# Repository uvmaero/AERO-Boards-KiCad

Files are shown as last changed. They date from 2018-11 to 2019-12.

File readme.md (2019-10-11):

# Readme

This repo was originally @willemcvu 's personal AERO boards repo. From 2019-20 onward it will be used by all of AERO to store boards designed for the AERO cars.

Some are finished and have been produced, tested, etc. Others have not. Up to you to figure out if a particular board might be useful for your needs.

If you do produce a board, let me know! I'd love to know what you're using it for.

Everything here is licensed under CC-BY-SA and thus is OSHWA-compliant.

# The Boards

(Often out-of-date) descriptions of what these boards do.

## BattMon

Monitors the current/voltage to/from a battery and power consumer. Includes a relay on the battery, ATMega328p, and CANBUS interface. This board has been produced and partially tested.
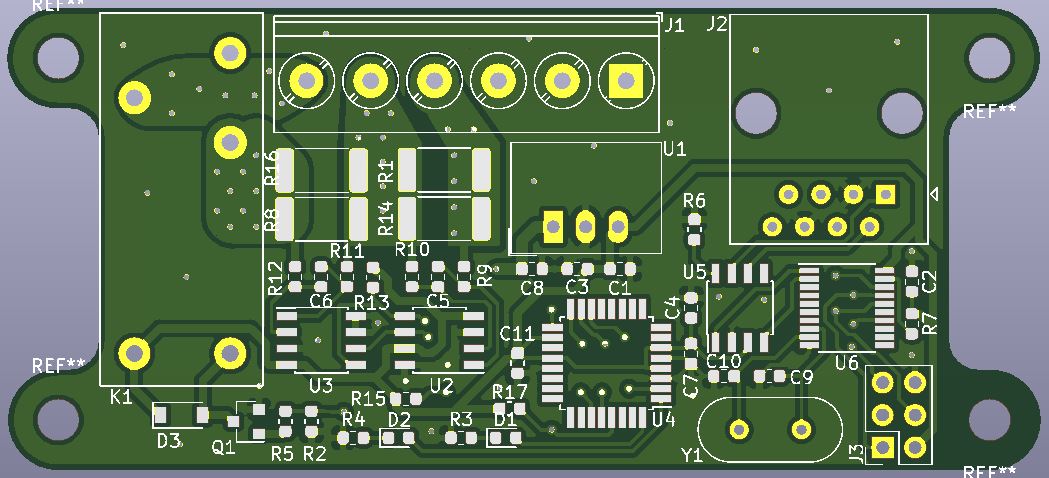
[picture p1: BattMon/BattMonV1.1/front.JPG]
Front BattMon

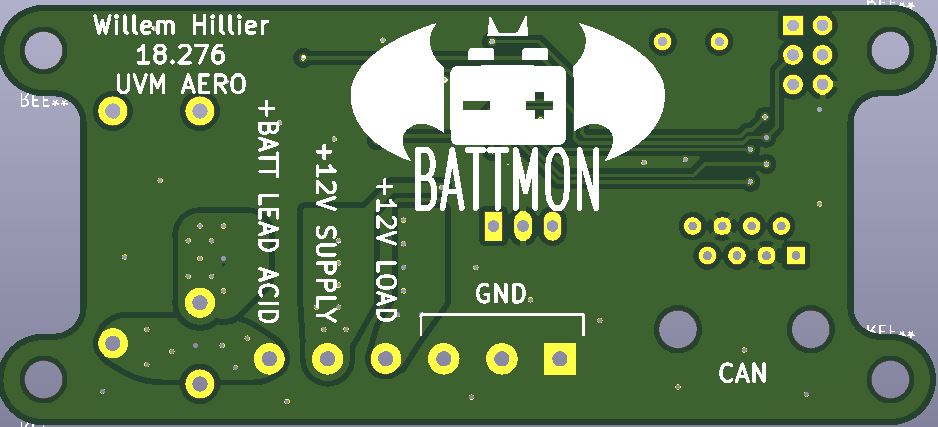
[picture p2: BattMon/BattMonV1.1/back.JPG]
Back BattMon


## CANShield
A generic Arduino Uno CANBUS shield. Once hooked up to an Uno, it is the same circuit used for all the boards with CANBUS+ATMega328p found here. Untested and unproduced.
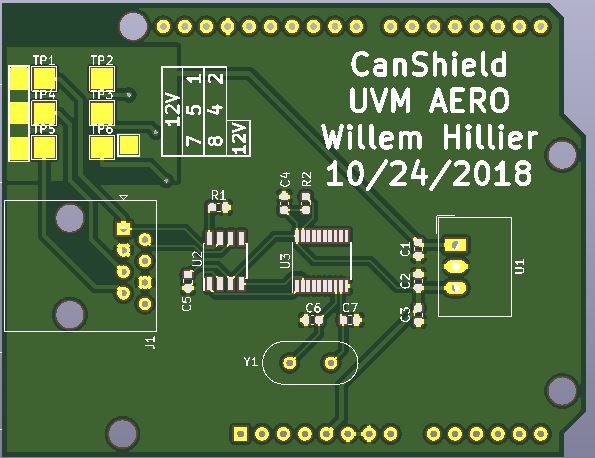
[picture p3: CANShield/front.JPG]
Front CanShield

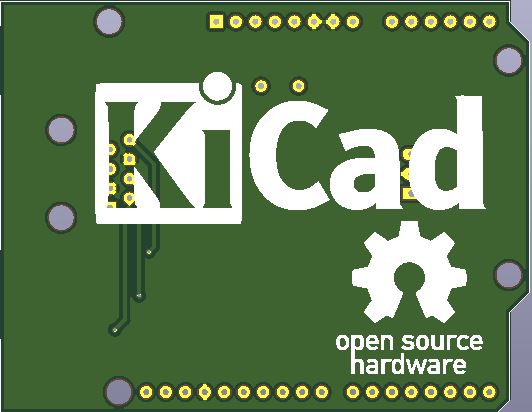
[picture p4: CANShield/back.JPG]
Back CanShield


## DC_DCBoard - Superseded by interface-board ("BigBoi")
Converts ~300VDC to ~12VDC using a DCM CHiP module from Vicor Power. Can do 400W peak, will dissapate almost 40W at that load, so it has a 19mm Vicor heatsink, model #(?can't remember).  Version 1 has clearance issues. Version 2 is an intermediate version with those issues mostly fixed. Version 3 is still be designed, and it will be the final version. None have been produced or tested, and all probably have issues (v1 and v2 have known issues, and v3 isn't finished).
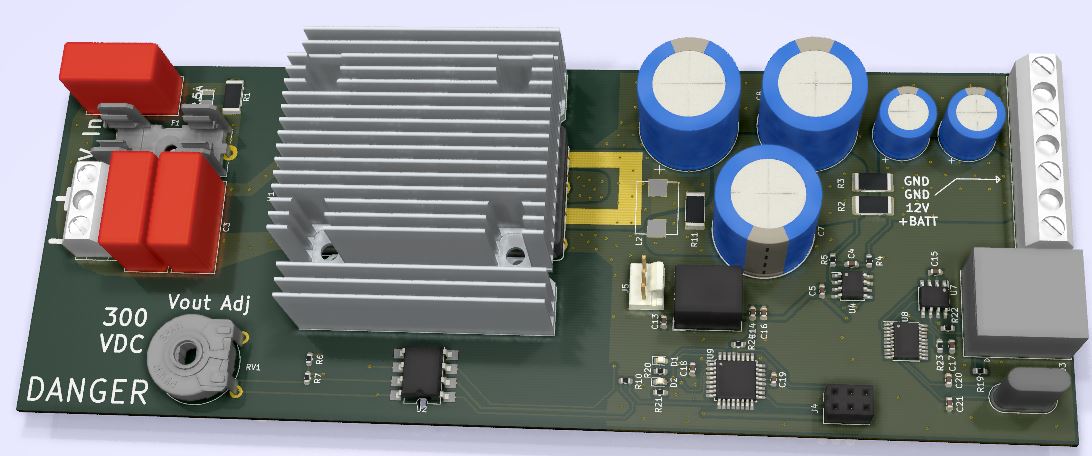
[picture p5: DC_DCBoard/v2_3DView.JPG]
DC_DCBoard


## FanBoy - Superseded by interface-board ("BigBoi")
Simple 4-channel PWM fan controller with ATMega328p and CANBUS interface. Tested, works great. Should be able to do ~15A a channel, although this hasn't been tested, and is probably not recommended.
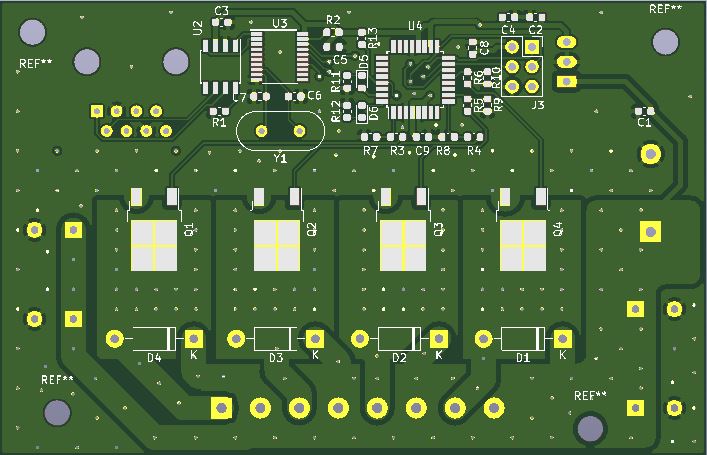
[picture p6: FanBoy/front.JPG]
Front FanBoy

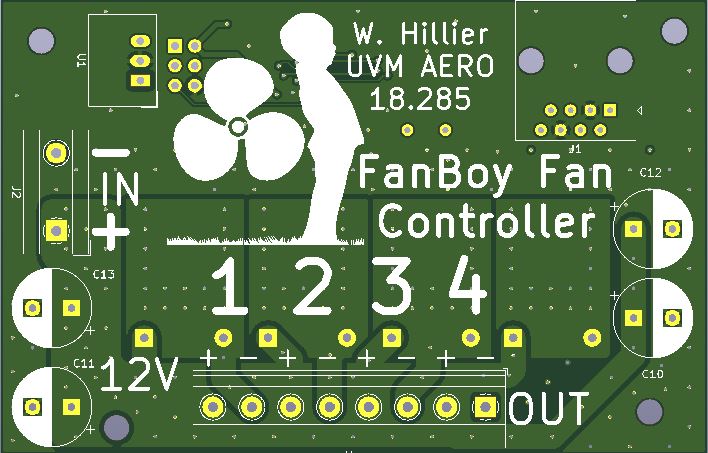
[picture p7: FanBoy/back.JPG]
Back FanBoy


## interface-board (aka "BigBoi")
Contains all the high-voltage interface circuitry. Hosts a Vicor DC/DC converter module that generates 12V for the entire car. Also controls fans, pump, and brakelight, and includes CANBUS interface, NTC inputs, and some assorted other functionality. "standoffs-biggerbox" is the current working version. Competition-tested, working 100%.
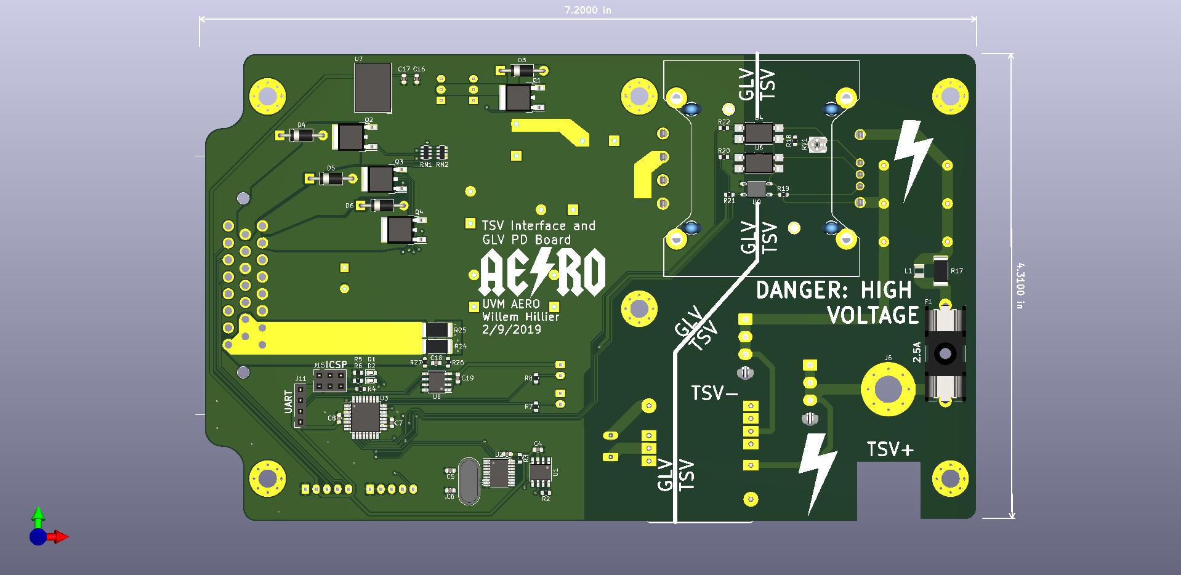
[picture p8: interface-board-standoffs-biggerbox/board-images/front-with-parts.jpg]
bigboi front


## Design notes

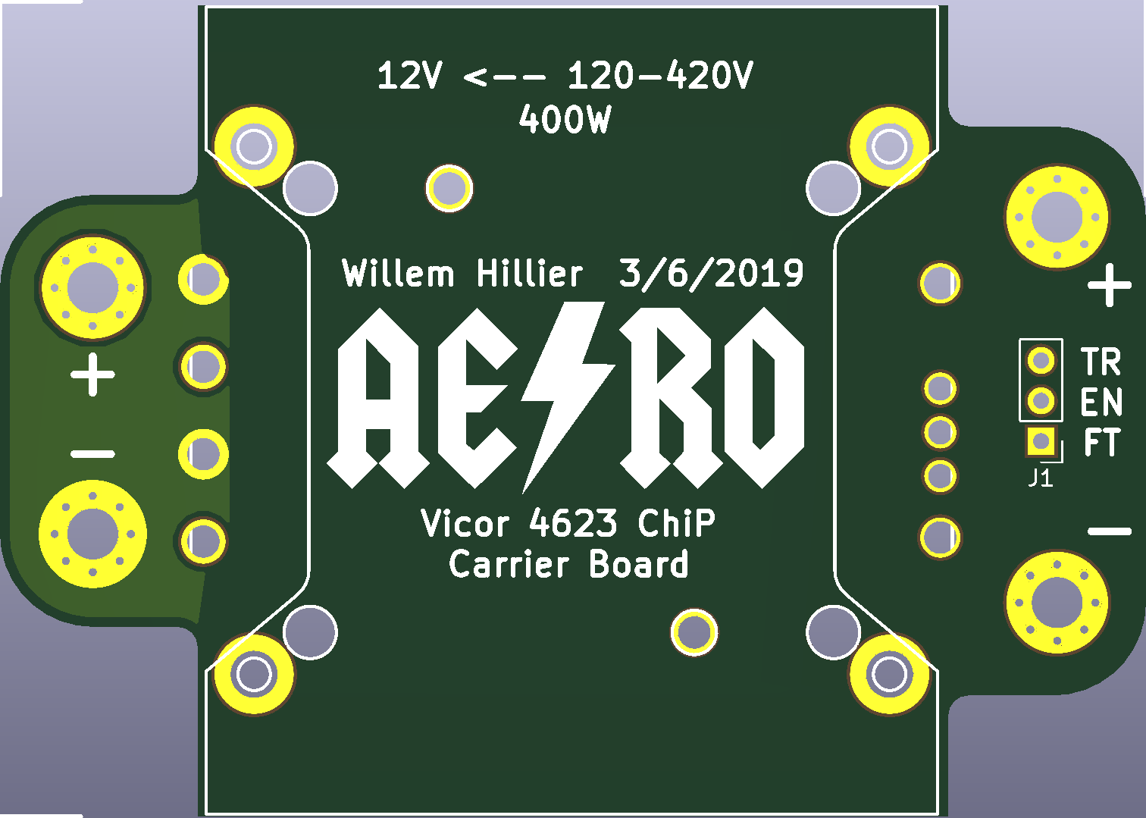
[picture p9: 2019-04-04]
vicor-socket/back.PNG

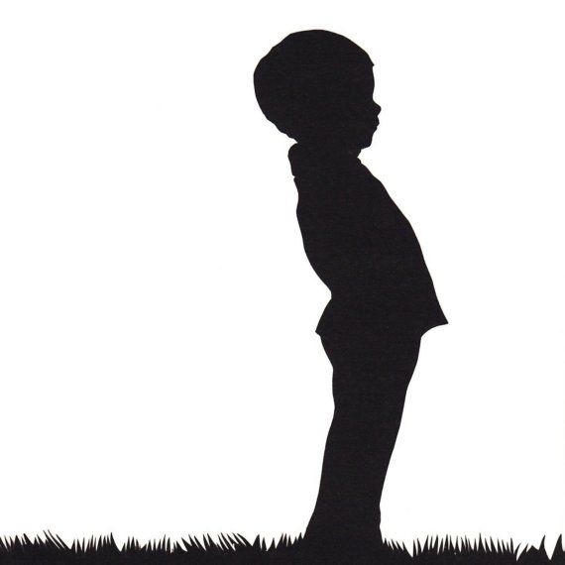
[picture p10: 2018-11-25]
FanBoy/boy.jpg

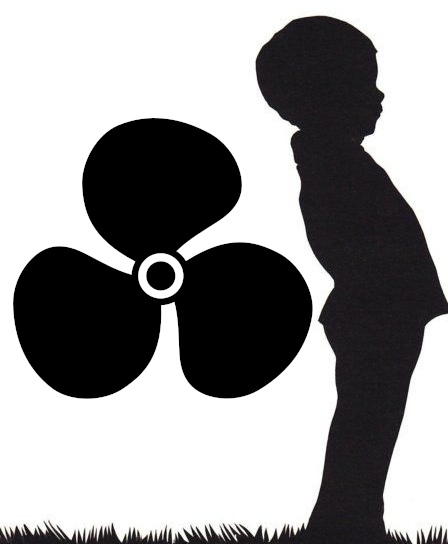
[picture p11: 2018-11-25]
FanBoy/fanboy.png

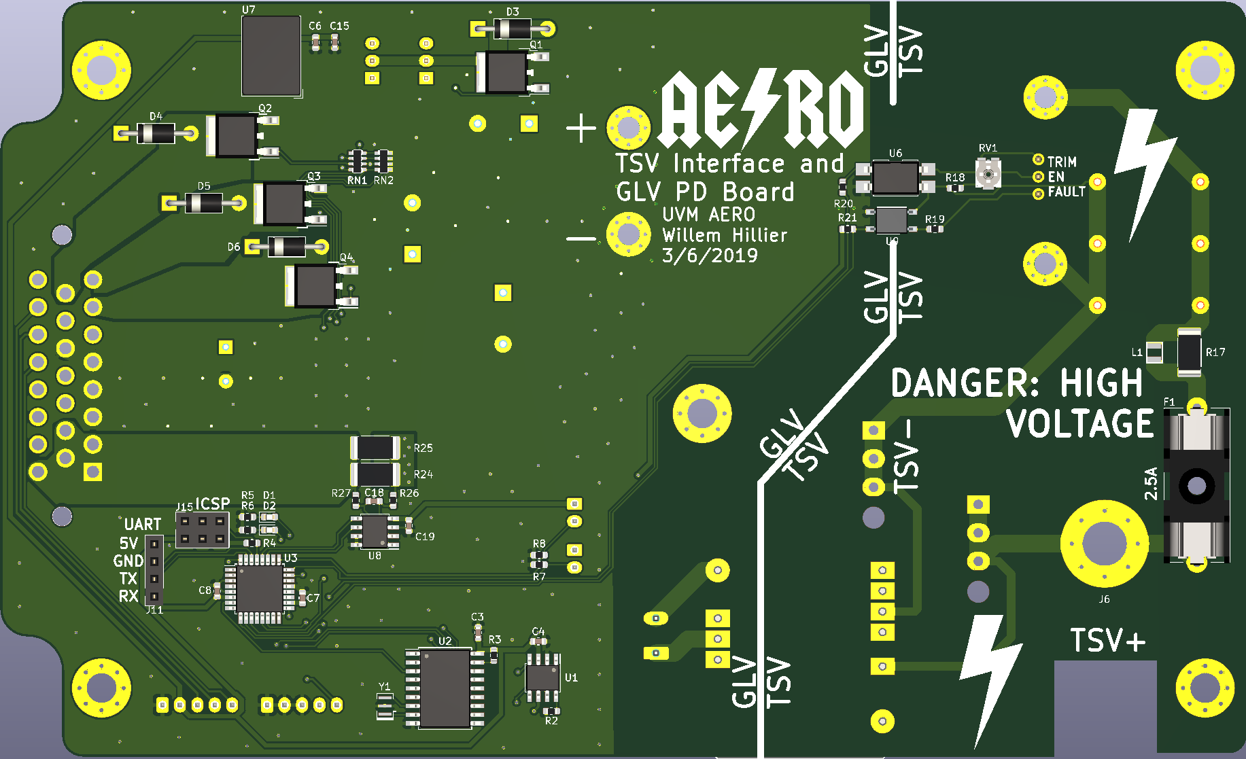
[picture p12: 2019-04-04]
interface-board-standoffs-biggerbox/front.PNG

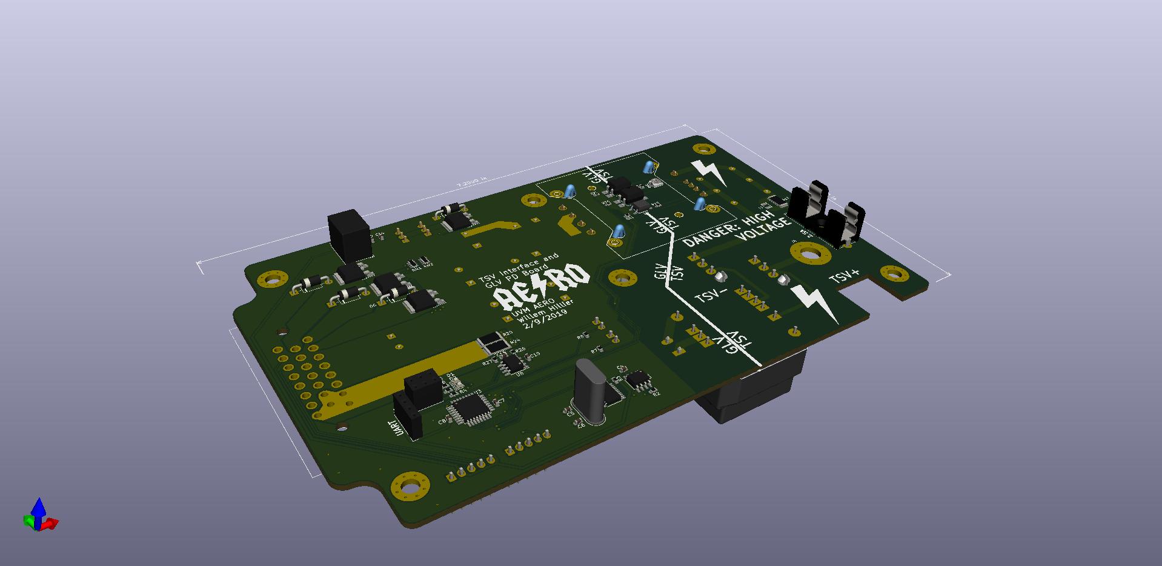
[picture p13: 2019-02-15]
interface-board-standoffs-biggerbox/board-images/front-3d.jpg

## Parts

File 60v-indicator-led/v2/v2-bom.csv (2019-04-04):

Id | Designator | Package | Quantity | Designation | Supplier and ref
1 | G***,G*** | AERO_Logo_15x6mm | 2 | LOGO
2 | D1 | LPA-C011301S-x LED 0805 LIGHT PIPE SINGLE VERT SMD | 1 | RED_LED
3 | R1,R2,R3,R4,R5,R6,R7,R8,R9,R10 | R_0805_2012Metric | 10 | 1k
4 | M3 | MountingHole_3.2mm_M3_DIN965 | 1 | MountingHole_3.2mm_M3_DIN965
5 | J1,J2 | TE_MATE-N-LOK_1-770866-x_1x02_P4.14mm_Vertical | 2 | Conn_01x02

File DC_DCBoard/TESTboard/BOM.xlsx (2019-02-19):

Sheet: Sheet1
Vendor | Found? | Digikey | Mouser | MPN | Quantity | ref | value5 | footprint | lib | part | description | names | tstamps6 | tstamp | datasheet | lib7 | part8 | description9 | docs | fp | field | name10 | num | name11 | type | alias | logical | uri | code | name12 | ref13 | pin
 | x |  |  |  | 1 | U1 | DCM4623TD2J13D0T70 | CustomFootprints:DCM4623TD2J13D0T70 w_landpattern | DC_DCBoard-rescue | DCM4623TD2J13D0T70-AEROParts |  | / | / | 5BDD1F41
 |  |  |  |  | 1 | R1 | 1Ω | Resistor_SMD:R_2512_6332Metric | Device | R_US | Resistor US symbol | / | / | 5BDD239A | ~
 | x |  |  | DFE252012P-1R0M=P2 | 1 | L1 | 1uH | CustomFootprints:Murata_DFE252012P_Inductor | Device | L_Small | Inductor, small symbol | / | / | 5BDD2418 | ~
 | x |  | https://www.mouser.com/ProductDetail/EPCOS-TDK/B32672P5684K000?qs=vvQZUlcHev%2F7kTLX0LjBgw%3D%3D | B32672P5684K000 | 3 | C1 | 0.68uF | Capacitor_THT:C_Rect_L18.0mm_W8.0mm_P15.00mm_FKS3_FKP3 | Device | C_Small | Unpolarized capacitor | / | / | 5BDD25B3 | ~
AERO | x |  |  |  | 3 | R6 | 1k | Resistor_SMD:R_0603_1608Metric | Device | R_US | Resistor US symbol | / | / | 5BDD58DC | ~
AERO | x |  |  |  | 1 | R9 | 10k | Resistor_SMD:R_0603_1608Metric | Device | R_US | Resistor US symbol | / | / | 5BDDACE2 | ~
AERO | x |  |  |  | 2 | C9 | 470uF | Capacitor_THT:CP_Radial_D10.0mm_P5.00mm | Device | C | Unpolarized capacitor | / | / | 5BDDF5C4 | ~
 | x |  |  | TC33X-2-503E | 1 | RV1 | 50k | CustomFootprints:TC33X-503ECT-ND | Device | R_POT_TRIM_US | Trim-Potentiometer US symbol | / | / | 5BF39F9A | ~
 |  |  |  | PA2607.151NLT | 1 | L2 | 0.15uH | CustomFootprints:PA2607 | Device | L_Small | Inductor, small symbol | / | / | 5BEEF7F2 | ~
 |  |  |  |  |  | R11 | 1Ω | Resistor_SMD:R_2512_6332Metric | Device | R_US | Resistor US symbol | / | / | 5BEF82F3 | ~
 |  |  |  |  | 3 | C6 | 4700uF | Capacitor_THT:CP_Radial_D18.0mm_P7.50mm | Device | C_Small | Unpolarized capacitor | / | / | 5BF35C23 | ~
 |  |  |  |  |  | J1 | TSV | TerminalBlock_MetzConnect:TerminalBlock_MetzConnect_Type067_RT01902HDWC_1x02_P10.00mm_Horizontal | Connector | Screw_Terminal_01x02 | Generic screw terminal, single row, 01x02, script generated (kicad-library-utils/schlib/autogen/connector/) | / | / | 5C19FA45 | ~
 |  |  |  |  |  | F1 | 2.5A | Fuse:Fuseholder_Cylinder-5x20mm_Schurter_0031_8201_Horizontal_Open | Device | Fuse_Small | Fuse, small symbol | / | / | 5C19FA4C | ~
 |  |  |  |  |  | J2 | 12V_OUT | TerminalBlock_MetzConnect:TerminalBlock_MetzConnect_Type067_RT01904HDWC_1x04_P10.00mm_Horizontal | Connector | Screw_Terminal_01x04 | Generic screw terminal, single row, 01x04, script generated (kicad-library-utils/schlib/autogen/connector/) | / | / | 5BDD1FC6 | ~
 |  |  |  |  |  | U3 | TLP184 | CustomFootprints:TLP182 | Isolator | TLP184 | AC/DC Optocoupler, Vce 80V, CTR 50-100%, MFSOP6 | / | / | 5C5A3E1C | https://toshiba.semicon-storage.com/info/docget.jsp?did=11793&prodName=TLP184
AERO | x |  |  |  | 2 | U2 | LTV-817S | Package_DIP:SMDIP-4_W9.53mm | Isolator | LTV-817S | DC Optocoupler, Vce 35V, CTR 50%, SMDIP-4 | / | / | 5C5B92F0 | http://www.us.liteon.com/downloads/LTV-817-827-847.PDF
 |  |  |  |  |  | J3 | Conn_01x05 | Connector_PinHeader_2.54mm:PinHeader_1x05_P2.54mm_Vertical | Connector_Generic | Conn_01x05 | Generic connector, single row, 01x05, script generated (kicad-library-utils/schlib/autogen/connector/) | / | / | 5C5BE583 | ~
 |  |  |  |  |  | R2 | 6.8k | Resistor_SMD:R_0603_1608Metric | Device | R_US | Resistor US symbol | / | / | 5C5B2FDF | ~
 |  |  |  |  |  |  |  |  |  |  |  |  |  |  |  | Connector | Screw_Terminal_01x02 | Generic screw terminal, single row, 01x02, script generated (kicad-library-utils/schlib/autogen/connector/) | ~ | TerminalBlock*:*
 |  |  |  |  |  |  |  |  |  |  |  |  |  |  |  | Connector | Screw_Terminal_01x02 | Generic screw terminal, single row, 01x02, script generated (kicad-library-utils/schlib/autogen/connector/) | ~ |  | J | Reference
 |  |  |  |  |  |  |  |  |  |  |  |  |  |  |  | Connector | Screw_Terminal_01x02 | Generic screw terminal, single row, 01x02, script generated (kicad-library-utils/schlib/autogen/connector/) | ~ |  | Screw_Terminal_01x02 | Value
 |  |  |  |  |  |  |  |  |  |  |  |  |  |  |  | Connector | Screw_Terminal_01x02 | Generic screw terminal, single row, 01x02, script generated (kicad-library-utils/schlib/autogen/connector/) | ~ |  |  |  | 1 | Pin_1 | passive
 |  |  |  |  |  |  |  |  |  |  |  |  |  |  |  | Connector | Screw_Terminal_01x02 | Generic screw terminal, single row, 01x02, script generated (kicad-library-utils/schlib/autogen/connector/) | ~ |  |  |  | 2 | Pin_2 | passive
 |  |  |  |  |  |  |  |  |  |  |  |  |  |  |  | Connector | Screw_Terminal_01x04 | Generic screw terminal, single row, 01x04, script generated (kicad-library-utils/schlib/autogen/connector/) | ~ | TerminalBlock*:*
 |  |  |  |  |  |  |  |  |  |  |  |  |  |  |  | Connector | Screw_Terminal_01x04 | Generic screw terminal, single row, 01x04, script generated (kicad-library-utils/schlib/autogen/connector/) | ~ |  | J | Reference
 |  |  |  |  |  |  |  |  |  |  |  |  |  |  |  | Connector | Screw_Terminal_01x04 | Generic screw terminal, single row, 01x04, script generated (kicad-library-utils/schlib/autogen/connector/) | ~ |  | Screw_Terminal_01x04 | Value
 |  |  |  |  |  |  |  |  |  |  |  |  |  |  |  | Connector | Screw_Terminal_01x04 | Generic screw terminal, single row, 01x04, script generated (kicad-library-utils/schlib/autogen/connector/) | ~ |  |  |  | 1 | Pin_1 | passive
 |  |  |  |  |  |  |  |  |  |  |  |  |  |  |  | Connector | Screw_Terminal_01x04 | Generic screw terminal, single row, 01x04, script generated (kicad-library-utils/schlib/autogen/connector/) | ~ |  |  |  | 2 | Pin_2 | passive
 |  |  |  |  |  |  |  |  |  |  |  |  |  |  |  | Connector | Screw_Terminal_01x04 | Generic screw terminal, single row, 01x04, script generated (kicad-library-utils/schlib/autogen/connector/) | ~ |  |  |  | 3 | Pin_3 | passive
 |  |  |  |  |  |  |  |  |  |  |  |  |  |  |  | Connector | Screw_Terminal_01x04 | Generic screw terminal, single row, 01x04, script generated (kicad-library-utils/schlib/autogen/connector/) | ~ |  |  |  | 4 | Pin_4 | passive
 |  |  |  |  |  |  |  |  |  |  |  |  |  |  |  | Connector_Generic | Conn_01x05 | Generic connector, single row, 01x05, script generated (kicad-library-utils/schlib/autogen/connector/) | ~ | Connector*:*_1x??_*
 |  |  |  |  |  |  |  |  |  |  |  |  |  |  |  | Connector_Generic | Conn_01x05 | Generic connector, single row, 01x05, script generated (kicad-library-utils/schlib/autogen/connector/) | ~ |  | J | Reference
 |  |  |  |  |  |  |  |  |  |  |  |  |  |  |  | Connector_Generic | Conn_01x05 | Generic connector, single row, 01x05, script generated (kicad-library-utils/schlib/autogen/connector/) | ~ |  | Conn_01x05 | Value
 |  |  |  |  |  |  |  |  |  |  |  |  |  |  |  | Connector_Generic | Conn_01x05 | Generic connector, single row, 01x05, script generated (kicad-library-utils/schlib/autogen/connector/) | ~ |  |  |  | 1 | Pin_1 | passive
 |  |  |  |  |  |  |  |  |  |  |  |  |  |  |  | Connector_Generic | Conn_01x05 | Generic connector, single row, 01x05, script generated (kicad-library-utils/schlib/autogen/connector/) | ~ |  |  |  | 2 | Pin_2 | passive
 |  |  |  |  |  |  |  |  |  |  |  |  |  |  |  | Connector_Generic | Conn_01x05 | Generic connector, single row, 01x05, script generated (kicad-library-utils/schlib/autogen/connector/) | ~ |  |  |  | 3 | Pin_3 | passive
 |  |  |  |  |  |  |  |  |  |  |  |  |  |  |  | Connector_Generic | Conn_01x05 | Generic connector, single row, 01x05, script generated (kicad-library-utils/schlib/autogen/connector/) | ~ |  |  |  | 4 | Pin_4 | passive
 |  |  |  |  |  |  |  |  |  |  |  |  |  |  |  | Connector_Generic | Conn_01x05 | Generic connector, single row, 01x05, script generated (kicad-library-utils/schlib/autogen/connector/) | ~ |  |  |  | 5 | Pin_5 | passive
 |  |  |  |  |  |  |  |  |  |  |  |  |  |  |  | DC_DCBoard-rescue | DCM4623TD2J13D0T70-AEROParts |  |  |  | U | Reference
 |  |  |  |  |  |  |  |  |  |  |  |  |  |  |  | DC_DCBoard-rescue | DCM4623TD2J13D0T70-AEROParts |  |  |  | DCM4623TD2J13D0T70-AEROParts | Value
 |  |  |  |  |  |  |  |  |  |  |  |  |  |  |  | DC_DCBoard-rescue | DCM4623TD2J13D0T70-AEROParts |  |  |  |  |  | 1 | +IN | power_in
 |  |  |  |  |  |  |  |  |  |  |  |  |  |  |  | DC_DCBoard-rescue | DCM4623TD2J13D0T70-AEROParts |  |  |  |  |  | 2 | TR | input
 |  |  |  |  |  |  |  |  |  |  |  |  |  |  |  | DC_DCBoard-rescue | DCM4623TD2J13D0T70-AEROParts |  |  |  |  |  | 3 | EN | input
 |  |  |  |  |  |  |  |  |  |  |  |  |  |  |  | DC_DCBoard-rescue | DCM4623TD2J13D0T70-AEROParts |  |  |  |  |  | 4 | FT | input
 |  |  |  |  |  |  |  |  |  |  |  |  |  |  |  | DC_DCBoard-rescue | DCM4623TD2J13D0T70-AEROParts |  |  |  |  |  | 5 | -IN | power_in
 |  |  |  |  |  |  |  |  |  |  |  |  |  |  |  | DC_DCBoard-rescue | DCM4623TD2J13D0T70-AEROParts |  |  |  |  |  | 6 | -OUT | power_out
 |  |  |  |  |  |  |  |  |  |  |  |  |  |  |  | DC_DCBoard-rescue | DCM4623TD2J13D0T70-AEROParts |  |  |  |  |  | 7 | +OUT | power_out
 |  |  |  |  |  |  |  |  |  |  |  |  |  |  |  | DC_DCBoard-rescue | DCM4623TD2J13D0T70-AEROParts |  |  |  |  |  | 8 | -OUT | power_out
 |  |  |  |  |  |  |  |  |  |  |  |  |  |  |  | DC_DCBoard-rescue | DCM4623TD2J13D0T70-AEROParts |  |  |  |  |  | 9 | +OUT | power_out
 |  |  |  |  |  |  |  |  |  |  |  |  |  |  |  | Device | C | Unpolarized capacitor | ~ | C_*
 |  |  |  |  |  |  |  |  |  |  |  |  |  |  |  | Device | C | Unpolarized capacitor | ~ |  | C | Reference
 |  |  |  |  |  |  |  |  |  |  |  |  |  |  |  | Device | C | Unpolarized capacitor | ~ |  | C | Value
 |  |  |  |  |  |  |  |  |  |  |  |  |  |  |  | Device | C | Unpolarized capacitor | ~ |  |  |  | 1 | ~ | passive
 |  |  |  |  |  |  |  |  |  |  |  |  |  |  |  | Device | C | Unpolarized capacitor | ~ |  |  |  | 2 | ~ | passive
 |  |  |  |  |  |  |  |  |  |  |  |  |  |  |  | Device | C_Small | Unpolarized capacitor | ~ | C_*
 |  |  |  |  |  |  |  |  |  |  |  |  |  |  |  | Device | C_Small | Unpolarized capacitor | ~ |  | C | Reference
 |  |  |  |  |  |  |  |  |  |  |  |  |  |  |  | Device | C_Small | Unpolarized capacitor | ~ |  | C_Small | Value
 |  |  |  |  |  |  |  |  |  |  |  |  |  |  |  | Device | C_Small | Unpolarized capacitor | ~ |  |  |  | 1 | ~ | passive
 |  |  |  |  |  |  |  |  |  |  |  |  |  |  |  | Device | C_Small | Unpolarized capacitor | ~ |  |  |  | 2 | ~ | passive
 |  |  |  |  |  |  |  |  |  |  |  |  |  |  |  | Device | Fuse_Small | Fuse, small symbol | ~ | SM*
 |  |  |  |  |  |  |  |  |  |  |  |  |  |  |  | Device | Fuse_Small | Fuse, small symbol | ~ |  | F | Reference
 |  |  |  |  |  |  |  |  |  |  |  |  |  |  |  | Device | Fuse_Small | Fuse, small symbol | ~ |  | Fuse_Small | Value
 |  |  |  |  |  |  |  |  |  |  |  |  |  |  |  | Device | Fuse_Small | Fuse, small symbol | ~ |  |  |  | 1 | ~ | passive
 |  |  |  |  |  |  |  |  |  |  |  |  |  |  |  | Device | Fuse_Small | Fuse, small symbol | ~ |  |  |  | 2 | ~ | passive
 |  |  |  |  |  |  |  |  |  |  |  |  |  |  |  | Device | L_Small | Inductor, small symbol | ~ | Choke_*
 |  |  |  |  |  |  |  |  |  |  |  |  |  |  |  | Device | L_Small | Inductor, small symbol | ~ | *Coil*
 |  |  |  |  |  |  |  |  |  |  |  |  |  |  |  | Device | L_Small | Inductor, small symbol | ~ | Inductor_*
 |  |  |  |  |  |  |  |  |  |  |  |  |  |  |  | Device | L_Small | Inductor, small symbol | ~ | L_*
 |  |  |  |  |  |  |  |  |  |  |  |  |  |  |  | Device | L_Small | Inductor, small symbol | ~ |  | L | Reference
 |  |  |  |  |  |  |  |  |  |  |  |  |  |  |  | Device | L_Small | Inductor, small symbol | ~ |  | L_Small | Value
 |  |  |  |  |  |  |  |  |  |  |  |  |  |  |  | Device | L_Small | Inductor, small symbol | ~ |  |  |  | 1 | ~ | passive
 |  |  |  |  |  |  |  |  |  |  |  |  |  |  |  | Device | L_Small | Inductor, small symbol | ~ |  |  |  | 2 | ~ | passive
 |  |  |  |  |  |  |  |  |  |  |  |  |  |  |  | Device | R_POT_TRIM_US | Trim-Potentiometer US symbol | ~ | Potentiometer*
 |  |  |  |  |  |  |  |  |  |  |  |  |  |  |  | Device | R_POT_TRIM_US | Trim-Potentiometer US symbol | ~ |  | RV | Reference
 |  |  |  |  |  |  |  |  |  |  |  |  |  |  |  | Device | R_POT_TRIM_US | Trim-Potentiometer US symbol | ~ |  | R_POT_TRIM_US | Value
 |  |  |  |  |  |  |  |  |  |  |  |  |  |  |  | Device | R_POT_TRIM_US | Trim-Potentiometer US symbol | ~ |  |  |  | 1 | 1 | passive
 |  |  |  |  |  |  |  |  |  |  |  |  |  |  |  | Device | R_POT_TRIM_US | Trim-Potentiometer US symbol | ~ |  |  |  | 2 | 2 | passive
 |  |  |  |  |  |  |  |  |  |  |  |  |  |  |  | Device | R_POT_TRIM_US | Trim-Potentiometer US symbol | ~ |  |  |  | 3 | 3 | passive
 |  |  |  |  |  |  |  |  |  |  |  |  |  |  |  | Device | R_US | Resistor US symbol | ~ | R_*
 |  |  |  |  |  |  |  |  |  |  |  |  |  |  |  | Device | R_US | Resistor US symbol | ~ |  | R | Reference
 |  |  |  |  |  |  |  |  |  |  |  |  |  |  |  | Device | R_US | Resistor US symbol | ~ |  | R_US | Value
 |  |  |  |  |  |  |  |  |  |  |  |  |  |  |  | Device | R_US | Resistor US symbol | ~ |  |  |  | 1 | ~ | passive
 |  |  |  |  |  |  |  |  |  |  |  |  |  |  |  | Device | R_US | Resistor US symbol | ~ |  |  |  | 2 | ~ | passive
 |  |  |  |  |  |  |  |  |  |  |  |  |  |  |  | Isolator | LTV-817S | DC Optocoupler, Vce 35V, CTR 50%, SMDIP-4 | http://www.us.liteon.com/downloads/LTV-817-827-847.PDF | SMDIP*W9.53mm*
 |  |  |  |  |  |  |  |  |  |  |  |  |  |  |  | Isolator | LTV-817S | DC Optocoupler, Vce 35V, CTR 50%, SMDIP-4 | http://www.us.liteon.com/downloads/LTV-817-827-847.PDF |  | U | Reference
 |  |  |  |  |  |  |  |  |  |  |  |  |  |  |  | Isolator | LTV-817S | DC Optocoupler, Vce 35V, CTR 50%, SMDIP-4 | http://www.us.liteon.com/downloads/LTV-817-827-847.PDF |  | LTV-817S | Value
 |  |  |  |  |  |  |  |  |  |  |  |  |  |  |  | Isolator | LTV-817S | DC Optocoupler, Vce 35V, CTR 50%, SMDIP-4 | http://www.us.liteon.com/downloads/LTV-817-827-847.PDF |  | Package_DIP:SMDIP-4_W9.53mm | Footprint
 |  |  |  |  |  |  |  |  |  |  |  |  |  |  |  | Isolator | LTV-817S | DC Optocoupler, Vce 35V, CTR 50%, SMDIP-4 | http://www.us.liteon.com/downloads/LTV-817-827-847.PDF |  |  |  | 1 | ~ | passive
 |  |  |  |  |  |  |  |  |  |  |  |  |  |  |  | Isolator | LTV-817S | DC Optocoupler, Vce 35V, CTR 50%, SMDIP-4 | http://www.us.liteon.com/downloads/LTV-817-827-847.PDF |  |  |  | 2 | ~ | passive
 |  |  |  |  |  |  |  |  |  |  |  |  |  |  |  | Isolator | LTV-817S | DC Optocoupler, Vce 35V, CTR 50%, SMDIP-4 | http://www.us.liteon.com/downloads/LTV-817-827-847.PDF |  |  |  | 3 | ~ | passive
 |  |  |  |  |  |  |  |  |  |  |  |  |  |  |  | Isolator | LTV-817S | DC Optocoupler, Vce 35V, CTR 50%, SMDIP-4 | http://www.us.liteon.com/downloads/LTV-817-827-847.PDF |  |  |  | 4 | ~ | passive
 |  |  |  |  |  |  |  |  |  |  |  |  |  |  |  | Isolator | TLP184 | AC/DC Optocoupler, Vce 80V, CTR 50-100%, MFSOP6 | https://toshiba.semicon-storage.com/info/docget.jsp?did=11793&prodName=TLP184 | MFSOP6*4.4x3.6mm*P1.27mm* |  |  |  |  |  | TLP184(SE
 |  |  |  |  |  |  |  |  |  |  |  |  |  |  |  | Isolator | TLP184 | AC/DC Optocoupler, Vce 80V, CTR 50-100%, MFSOP6 | https://toshiba.semicon-storage.com/info/docget.jsp?did=11793&prodName=TLP184 |  | U | Reference |  |  |  | TLP184(SE
 |  |  |  |  |  |  |  |  |  |  |  |  |  |  |  | Isolator | TLP184 | AC/DC Optocoupler, Vce 80V, CTR 50-100%, MFSOP6 | https://toshiba.semicon-storage.com/info/docget.jsp?did=11793&prodName=TLP184 |  | TLP184 | Value |  |  |  | TLP184(SE
 |  |  |  |  |  |  |  |  |  |  |  |  |  |  |  | Isolator | TLP184 | AC/DC Optocoupler, Vce 80V, CTR 50-100%, MFSOP6 | https://toshiba.semicon-storage.com/info/docget.jsp?did=11793&prodName=TLP184 |  | Package_SO:MFSOP6-4_4.4x3.6mm_P1.27mm | Footprint |  |  |  | TLP184(SE
 |  |  |  |  |  |  |  |  |  |  |  |  |  |  |  | Isolator | TLP184 | AC/DC Optocoupler, Vce 80V, CTR 50-100%, MFSOP6 | https://toshiba.semicon-storage.com/info/docget.jsp?did=11793&prodName=TLP184 |  |  |  | 1 | ~ | passive | TLP184(SE
 |  |  |  |  |  |  |  |  |  |  |  |  |  |  |  | Isolator | TLP184 | AC/DC Optocoupler, Vce 80V, CTR 50-100%, MFSOP6 | https://toshiba.semicon-storage.com/info/docget.jsp?did=11793&prodName=TLP184 |  |  |  | 3 | ~ | passive | TLP184(SE
 |  |  |  |  |  |  |  |  |  |  |  |  |  |  |  | Isolator | TLP184 | AC/DC Optocoupler, Vce 80V, CTR 50-100%, MFSOP6 | https://toshiba.semicon-storage.com/info/docget.jsp?did=11793&prodName=TLP184 |  |  |  | 4 | ~ | passive | TLP184(SE
 |  |  |  |  |  |  |  |  |  |  |  |  |  |  |  | Isolator | TLP184 | AC/DC Optocoupler, Vce 80V, CTR 50-100%, MFSOP6 | https://toshiba.semicon-storage.com/info/docget.jsp?did=11793&prodName=TLP184 |  |  |  | 6 | ~ | passive | TLP184(SE
 |  |  |  |  |  |  |  |  |  |  |  |  |  |  |  |  |  |  |  |  |  |  |  |  |  |  | Connector | C:\Program Files\KiCad\share\kicad\library/Connector.lib
 |  |  |  |  |  |  |  |  |  |  |  |  |  |  |  |  |  |  |  |  |  |  |  |  |  |  | Connector_Generic | C:\Program Files\KiCad\share\kicad\library/Connector_Generic.lib
 |  |  |  |  |  |  |  |  |  |  |  |  |  |  |  |  |  |  |  |  |  |  |  |  |  |  | DC_DCBoard-rescue | C:\Users\Willem Hillier\Documents\GitHub\AERO-Boards-KiCad\DC_DCBoard\TESTboard/DC_DCBoard-rescue.lib
 |  |  |  |  |  |  |  |  |  |  |  |  |  |  |  |  |  |  |  |  |  |  |  |  |  |  | Device | C:\Program Files\KiCad\share\kicad\library/Device.lib
 |  |  |  |  |  |  |  |  |  |  |  |  |  |  |  |  |  |  |  |  |  |  |  |  |  |  | Isolator | C:\Program Files\KiCad\share\kicad\library/Isolator.lib
 |  |  |  |  |  |  |  |  |  |  |  |  |  |  |  |  |  |  |  |  |  |  |  |  |  |  |  |  | 1 | GND | J3 | 5
 |  |  |  |  |  |  |  |  |  |  |  |  |  |  |  |  |  |  |  |  |  |  |  |  |  |  |  |  | 1 | GND | U1 | 8
 |  |  |  |  |  |  |  |  |  |  |  |  |  |  |  |  |  |  |  |  |  |  |  |  |  |  |  |  | 1 | GND | U4 | 2
 |  |  |  |  |  |  |  |  |  |  |  |  |  |  |  |  |  |  |  |  |  |  |  |  |  |  |  |  | 1 | GND | U2 | 2
 |  |  |  |  |  |  |  |  |  |  |  |  |  |  |  |  |  |  |  |  |  |  |  |  |  |  |  |  | 1 | GND | U3 | 4
 |  |  |  |  |  |  |  |  |  |  |  |  |  |  |  |  |  |  |  |  |  |  |  |  |  |  |  |  | 1 | GND | J2 | 4
 |  |  |  |  |  |  |  |  |  |  |  |  |  |  |  |  |  |  |  |  |  |  |  |  |  |  |  |  | 1 | GND | J2 | 3
 |  |  |  |  |  |  |  |  |  |  |  |  |  |  |  |  |  |  |  |  |  |  |  |  |  |  |  |  | 1 | GND | U1 | 6
 |  |  |  |  |  |  |  |  |  |  |  |  |  |  |  |  |  |  |  |  |  |  |  |  |  |  |  |  | 1 | GND | C7 | 2
 |  |  |  |  |  |  |  |  |  |  |  |  |  |  |  |  |  |  |  |  |  |  |  |  |  |  |  |  | 1 | GND | C8 | 2
 |  |  |  |  |  |  |  |  |  |  |  |  |  |  |  |  |  |  |  |  |  |  |  |  |  |  |  |  | 1 | GND | C11 | 2
 |  |  |  |  |  |  |  |  |  |  |  |  |  |  |  |  |  |  |  |  |  |  |  |  |  |  |  |  | 1 | GND | C6 | 2
 |  |  |  |  |  |  |  |  |  |  |  |  |  |  |  |  |  |  |  |  |  |  |  |  |  |  |  |  | 1 | GND | C9 | 2
 |  |  |  |  |  |  |  |  |  |  |  |  |  |  |  |  |  |  |  |  |  |  |  |  |  |  |  |  | 2 | Net-(F1-Pad1) | F1 | 1
 |  |  |  |  |  |  |  |  |  |  |  |  |  |  |  |  |  |  |  |  |  |  |  |  |  |  |  |  | 2 | Net-(F1-Pad1) | J1 | 1
 |  |  |  |  |  |  |  |  |  |  |  |  |  |  |  |  |  |  |  |  |  |  |  |  |  |  |  |  | 3 | /HV+ | F1 | 2
 |  |  |  |  |  |  |  |  |  |  |  |  |  |  |  |  |  |  |  |  |  |  |  |  |  |  |  |  | 3 | /HV+ | L1 | 1
 |  |  |  |  |  |  |  |  |  |  |  |  |  |  |  |  |  |  |  |  |  |  |  |  |  |  |  |  | 3 | /HV+ | R1 | 2
 |  |  |  |  |  |  |  |  |  |  |  |  |  |  |  |  |  |  |  |  |  |  |  |  |  |  |  |  | 4 | /HV- | C3 | 2
 |  |  |  |  |  |  |  |  |  |  |  |  |  |  |  |  |  |  |  |  |  |  |  |  |  |  |  |  | 4 | /HV- | U2 | 3
 |  |  |  |  |  |  |  |  |  |  |  |  |  |  |  |  |  |  |  |  |  |  |  |  |  |  |  |  | 4 | /HV- | U3 | 3
 |  |  |  |  |  |  |  |  |  |  |  |  |  |  |  |  |  |  |  |  |  |  |  |  |  |  |  |  | 4 | /HV- | C1 | 2
 |  |  |  |  |  |  |  |  |  |  |  |  |  |  |  |  |  |  |  |  |  |  |  |  |  |  |  |  | 4 | /HV- | J1 | 2
 |  |  |  |  |  |  |  |  |  |  |  |  |  |  |  |  |  |  |  |  |  |  |  |  |  |  |  |  | 4 | /HV- | U4 | 3
 |  |  |  |  |  |  |  |  |  |  |  |  |  |  |  |  |  |  |  |  |  |  |  |  |  |  |  |  | 4 | /HV- | C2 | 2
 |  |  |  |  |  |  |  |  |  |  |  |  |  |  |  |  |  |  |  |  |  |  |  |  |  |  |  |  | 4 | /HV- | R2 | 2
 |  |  |  |  |  |  |  |  |  |  |  |  |  |  |  |  |  |  |  |  |  |  |  |  |  |  |  |  | 4 | /HV- | U1 | 5
 |  |  |  |  |  |  |  |  |  |  |  |  |  |  |  |  |  |  |  |  |  |  |  |  |  |  |  |  | 5 | Net-(R2-Pad1) | R2 | 1
 |  |  |  |  |  |  |  |  |  |  |  |  |  |  |  |  |  |  |  |  |  |  |  |  |  |  |  |  | 5 | Net-(R2-Pad1) | RV1 | 2
 |  |  |  |  |  |  |  |  |  |  |  |  |  |  |  |  |  |  |  |  |  |  |  |  |  |  |  |  | 6 | +12V | C11 | 1
 |  |  |  |  |  |  |  |  |  |  |  |  |  |  |  |  |  |  |  |  |  |  |  |  |  |  |  |  | 6 | +12V | C7 | 1
 |  |  |  |  |  |  |  |  |  |  |  |  |  |  |  |  |  |  |  |  |  |  |  |  |  |  |  |  | 6 | +12V | C9 | 1
 |  |  |  |  |  |  |  |  |  |  |  |  |  |  |  |  |  |  |  |  |  |  |  |  |  |  |  |  | 6 | +12V | C8 | 1
 |  |  |  |  |  |  |  |  |  |  |  |  |  |  |  |  |  |  |  |  |  |  |  |  |  |  |  |  | 6 | +12V | L2 | 2
 |  |  |  |  |  |  |  |  |  |  |  |  |  |  |  |  |  |  |  |  |  |  |  |  |  |  |  |  | 6 | +12V | R11 | 1
 |  |  |  |  |  |  |  |  |  |  |  |  |  |  |  |  |  |  |  |  |  |  |  |  |  |  |  |  | 6 | +12V | J2 | 1
 |  |  |  |  |  |  |  |  |  |  |  |  |  |  |  |  |  |  |  |  |  |  |  |  |  |  |  |  | 6 | +12V | J2 | 2
 |  |  |  |  |  |  |  |  |  |  |  |  |  |  |  |  |  |  |  |  |  |  |  |  |  |  |  |  | 7 | Net-(C6-Pad1) | U1 | 9
 |  |  |  |  |  |  |  |  |  |  |  |  |  |  |  |  |  |  |  |  |  |  |  |  |  |  |  |  | 7 | Net-(C6-Pad1) | U1 | 7
 |  |  |  |  |  |  |  |  |  |  |  |  |  |  |  |  |  |  |  |  |  |  |  |  |  |  |  |  | 7 | Net-(C6-Pad1) | R11 | 2
 |  |  |  |  |  |  |  |  |  |  |  |  |  |  |  |  |  |  |  |  |  |  |  |  |  |  |  |  | 7 | Net-(C6-Pad1) | C6 | 1
 |  |  |  |  |  |  |  |  |  |  |  |  |  |  |  |  |  |  |  |  |  |  |  |  |  |  |  |  | 7 | Net-(C6-Pad1) | L2 | 1
 |  |  |  |  |  |  |  |  |  |  |  |  |  |  |  |  |  |  |  |  |  |  |  |  |  |  |  |  | 8 | +5V | J3 | 1
 |  |  |  |  |  |  |  |  |  |  |  |  |  |  |  |  |  |  |  |  |  |  |  |  |  |  |  |  | 8 | +5V | R9 | 2
 |  |  |  |  |  |  |  |  |  |  |  |  |  |  |  |  |  |  |  |  |  |  |  |  |  |  |  |  | 9 | /TRIM_EN | R10 | 1
 |  |  |  |  |  |  |  |  |  |  |  |  |  |  |  |  |  |  |  |  |  |  |  |  |  |  |  |  | 9 | /TRIM_EN | J3 | 2
 |  |  |  |  |  |  |  |  |  |  |  |  |  |  |  |  |  |  |  |  |  |  |  |  |  |  |  |  | 10 | /DC_DC_EN | R8 | 1
 |  |  |  |  |  |  |  |  |  |  |  |  |  |  |  |  |  |  |  |  |  |  |  |  |  |  |  |  | 10 | /DC_DC_EN | J3 | 3
 |  |  |  |  |  |  |  |  |  |  |  |  |  |  |  |  |  |  |  |  |  |  |  |  |  |  |  |  | 11 | /DC_DC_FAULT | U3 | 6
 |  |  |  |  |  |  |  |  |  |  |  |  |  |  |  |  |  |  |  |  |  |  |  |  |  |  |  |  | 11 | /DC_DC_FAULT | R9 | 1
 |  |  |  |  |  |  |  |  |  |  |  |  |  |  |  |  |  |  |  |  |  |  |  |  |  |  |  |  | 11 | /DC_DC_FAULT | J3 | 4
 |  |  |  |  |  |  |  |  |  |  |  |  |  |  |  |  |  |  |  |  |  |  |  |  |  |  |  |  | 12 | Net-(R6-Pad1) | U3 | 1
 |  |  |  |  |  |  |  |  |  |  |  |  |  |  |  |  |  |  |  |  |  |  |  |  |  |  |  |  | 12 | Net-(R6-Pad1) | R6 | 1
 |  |  |  |  |  |  |  |  |  |  |  |  |  |  |  |  |  |  |  |  |  |  |  |  |  |  |  |  | 13 | /TRIM | RV1 | 3
 |  |  |  |  |  |  |  |  |  |  |  |  |  |  |  |  |  |  |  |  |  |  |  |  |  |  |  |  | 13 | /TRIM | U1 | 2
 |  |  |  |  |  |  |  |  |  |  |  |  |  |  |  |  |  |  |  |  |  |  |  |  |  |  |  |  | 13 | /TRIM | U2 | 4
 |  |  |  |  |  |  |  |  |  |  |  |  |  |  |  |  |  |  |  |  |  |  |  |  |  |  |  |  | 14 | Net-(R8-Pad2) | U4 | 1
 |  |  |  |  |  |  |  |  |  |  |  |  |  |  |  |  |  |  |  |  |  |  |  |  |  |  |  |  | 14 | Net-(R8-Pad2) | R8 | 2
 |  |  |  |  |  |  |  |  |  |  |  |  |  |  |  |  |  |  |  |  |  |  |  |  |  |  |  |  | 15 | Net-(C1-Pad1) | C3 | 1
 |  |  |  |  |  |  |  |  |  |  |  |  |  |  |  |  |  |  |  |  |  |  |  |  |  |  |  |  | 15 | Net-(C1-Pad1) | C2 | 1
 |  |  |  |  |  |  |  |  |  |  |  |  |  |  |  |  |  |  |  |  |  |  |  |  |  |  |  |  | 15 | Net-(C1-Pad1) | U1 | 1
 |  |  |  |  |  |  |  |  |  |  |  |  |  |  |  |  |  |  |  |  |  |  |  |  |  |  |  |  | 15 | Net-(C1-Pad1) | R1 | 1
 |  |  |  |  |  |  |  |  |  |  |  |  |  |  |  |  |  |  |  |  |  |  |  |  |  |  |  |  | 15 | Net-(C1-Pad1) | C1 | 1
 |  |  |  |  |  |  |  |  |  |  |  |  |  |  |  |  |  |  |  |  |  |  |  |  |  |  |  |  | 15 | Net-(C1-Pad1) | L1 | 2
 |  |  |  |  |  |  |  |  |  |  |  |  |  |  |  |  |  |  |  |  |  |  |  |  |  |  |  |  | 16 | /FAULT | R6 | 2
 |  |  |  |  |  |  |  |  |  |  |  |  |  |  |  |  |  |  |  |  |  |  |  |  |  |  |  |  | 16 | /FAULT | U1 | 4
 |  |  |  |  |  |  |  |  |  |  |  |  |  |  |  |  |  |  |  |  |  |  |  |  |  |  |  |  | 17 | /EN | U4 | 4
 |  |  |  |  |  |  |  |  |  |  |  |  |  |  |  |  |  |  |  |  |  |  |  |  |  |  |  |  | 17 | /EN | U1 | 3
 |  |  |  |  |  |  |  |  |  |  |  |  |  |  |  |  |  |  |  |  |  |  |  |  |  |  |  |  | 18 | Net-(R10-Pad2) | U2 | 1
 |  |  |  |  |  |  |  |  |  |  |  |  |  |  |  |  |  |  |  |  |  |  |  |  |  |  |  |  | 18 | Net-(R10-Pad2) | R10 | 2
 |  |  |  |  |  |  |  |  |  |  |  |  |  |  |  |  |  |  |  |  |  |  |  |  |  |  |  |  | 19 | Net-(RV1-Pad1) | RV1 | 1

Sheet: Sheet2
MPN | Quantity
B32672P5684K000 | 3
DFE252012P-1R0M=P2 | 1

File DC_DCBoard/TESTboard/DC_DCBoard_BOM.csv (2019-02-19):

Id | Designator | Package | Quantity | Designation | Supplier and ref
1 | F1 | Fuseholder_Cylinder-5x20mm_Schurter_0031_8201_Horizontal_Open_3d | 1 | 2.5A
2 | U1 | DCM4623TD2J13D0T70_w_landpattern | 1 | DCM4623TD2J13D0T70
3 | REF**,REF**,REF**,REF** | MountingHole_4.3mm_M4 | 4 | MountingHole_4.3mm_M4
4 | C1,C2,C3 | C_Rect_L18.0mm_W8.0mm_P15.00mm_FKS3_FKP3 | 3 | 0.68uF
5 | C6,C7,C8 | CP_Radial_D18.0mm_P7.50mm | 3 | 4700uF
6 | C9,C11 | CP_Radial_D10.0mm_P5.00mm | 2 | 470uF
7 | J1 | TerminalBlock_MetzConnect_Type067_RT01902HDWC_1x02_P10.00mm_Horizontal | 1 | TSV
8 | J2 | TerminalBlock_MetzConnect_Type067_RT01904HDWC_1x04_P10.00mm_Horizontal | 1 | 12V_OUT
9 | L1 | Murata_DFE252012P_Inductor | 1 | 1uH
10 | L2 | PA2607 | 1 | 0.15uH
11 | R1,R11 | R_2512_6332Metric | 2 | 1Ω
12 | R6,R8,R10 | R_0603_1608Metric | 3 | 1k
13 | R9 | R_0603_1608Metric | 1 | 10k
14 | U2,U4 | SMDIP-4_W9.53mm | 2 | LTV-817S
15 | J3 | PinHeader_1x05_P2.54mm_Vertical | 1 | Conn_01x05
16 | R2 | R_0603_1608Metric | 1 | 6.8k
17 | G*** | hvlightningsymbol | 1 | LOGO
18 | RV1 | TC33X-503ECT-ND | 1 | 50k
19 | U3 | TLP182 | 1 | TLP184

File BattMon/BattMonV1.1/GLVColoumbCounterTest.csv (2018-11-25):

Id | Designator | Package | Quantity | Designation | Supplier and ref
1 | REF**,REF**,REF**,REF** | MountingHole_3.2mm_M3 | 4 | MountingHole_3.2mm_M3
2 | K1 | G2RL | 1 | G5V-1
3 | U4 | TQFP-32_7x7mm_P0.8mm | 1 | ATmega328P-AU
4 | J2 | RJ45_Amphenol_54602-x08_Horizontal | 1 | RJ45
5 | C1,C2,C4,C5,C6,C7,C11 | C_0603_1608Metric | 7 | 0.1uF
6 | C3,C8 | C_0603_1608Metric | 2 | 10uF
7 | D1,D2 | LED_0603_1608Metric | 2 | LED
8 | J1 | TerminalBlock_Phoenix_PT-1,5-6-5.0-H_1x06_P5.00mm_Horizontal | 1 | 12V_INTERFACE
9 | Q1 | SOT-23 | 1 | MMBT222A
10 | R2 | R_0603_1608Metric | 1 | 100k
11 | R3,R4,R5 | R_0603_1608Metric | 3 | 1k
12 | R6,R7,R15,R17 | R_0603_1608Metric | 4 | 10k
13 | R9,R10,R11,R12 | R_0603_1608Metric | 4 | 10
14 | R13 | R_0603_1608Metric | 1 | 10K
15 | U1 | Converter_DCDC_RECOM_R-78E-0.5_THT | 1 | R-78E5.0-0.5
16 | U2,U3 | SOIC-8_3.9x4.9mm_P1.27mm | 2 | INA219
17 | U5 | SOIC-8_3.9x4.9mm_P1.27mm | 1 | MCP2551-I-SN
18 | U6 | TSSOP-20_4.4x6.5mm_P0.65mm | 1 | MCP2515-IST
19 | C9,C10 | C_0603_1608Metric | 2 | 22pF
20 | R1,R8,R14,R16 | R_2512_6332Metric | 4 | 0.02
21 | J3 | PinSocket_2x03_P2.54mm_Vertical | 1 | Conn_02x03_Odd_Even
22 | D3 | D_SOD-123 | 1 | 1N4148
23 | Y1 | Crystal_HC49-U_Vertical | 1 | 8MHz
24 | G*** | batmonLogo | 1 | LOGO

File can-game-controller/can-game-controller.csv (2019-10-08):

Id | Designator | Package | Quantity | Designation | Supplier and ref
1 | J6 | PinHeader_2x03_P2.54mm_Vertical | 1 | Conn_02x03_Odd_Even
2 | C1,C2,C5,C6 | C_0603_1608Metric | 4 | 0.1uF
3 | C3,C4 | C_0603_1608Metric | 2 | 22pF
4 | C7,C8 | C_0603_1608Metric | 2 | 22p
5 | C9 | C_0603_1608Metric | 1 | 1u
6 | D1,D2 | LED_0603_1608Metric | 2 | LED
7 | FB1,FB2 | L_0805_2012Metric | 2 | MH2029-300Y
8 | J1 | RJ45_Amphenol_54602-x08_Horizontal | 1 | RJ45
9 | J2 | USB_B_OST_USB-B1HSxx_Horizontal | 1 | USB_B
10 | J3 | JST_PH_B8B-PH-K_1x08_P2.00mm_Vertical | 1 | Pots
11 | J4 | JST_PH_B8B-PH-K_1x08_P2.00mm_Vertical | 1 | Btns1
12 | J5 | JST_PH_B8B-PH-K_1x08_P2.00mm_Vertical | 1 | Btns2
13 | R1,R2,R4 | R_0603_1608Metric | 3 | 10k
14 | R3 | R_0603_1608Metric | 1 | 1M
15 | R5,R6 | R_0603_1608Metric | 2 | 1k
16 | U1 | SOIC-8_3.9x4.9mm_P1.27mm | 1 | MCP2551-I-SN
17 | U2 | SOIC-18W_7.5x11.6mm_P1.27mm | 1 | MCP2515-xSO
18 | U3 | TQFP-44_10x10mm_P0.8mm | 1 | ATmega32U4-AU
19 | Y1 | Crystal_HC49-U_Vertical | 1 | 8MHz
20 | Y2 | Resonator_SMD_muRata_CSTxExxV-3Pin_3.0x1.1mm | 1 | 16MHz

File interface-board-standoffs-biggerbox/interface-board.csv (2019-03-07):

Id | Designator | Package | Quantity | Designation | Supplier and ref
1 | J6 | MountingHole_6.4mm_M6_Pad_Via | 1 | HV+
2 | G***,G*** | AERO_Logo_30x12mm | 2 | LOGO
3 | U5 | vicor-socket-no-cutouts | 1 | DCM4623TD2J13D0T70
4 | U9 | TLP182 | 1 | TLP184
5 | RV1 | TC33X-503ECT-ND | 1 | 50k
6 | J16 | TE_1-776087-1 | 1 | AMPSEAL
7 | J11 | PinSocket_1x04_P2.54mm_Vertical | 1 | UART
8 | G***,G***,G*** | hvlightningsymbol | 3 | LOGO
9 | U10 | EPM1510SJ | 1 | EPM1510SJ
10 | REF**,REF**,REF**,REF**,REF** | MountingHole_4.3mm_M4_Pad_Via | 5 | MountingHole_4.3mm_M4_Pad_Via
11 | C3,C4,C7,C8,C18,C19,C6 | C_0603_1608Metric | 7 | 0.1uF
12 | C9,C10,C11 | C_Rect_L18.0mm_W8.0mm_P15.00mm_FKS3_FKP3 | 3 | 0.68uF
13 | C13,C14,C2 | CP_Radial_D18.0mm_P7.50mm | 3 | 4700uF
14 | C15,C5 | C_0603_1608Metric | 2 | 10uF
15 | D1,D2 | LED_0603_1608Metric | 2 | LED
16 | D3,D4,D5,D6 | D_DO-41_SOD81_P10.16mm_Horizontal | 4 | 1N4001
17 | J1 | Molex_KK-254_AE-6410-05A_1x05_P2.54mm_Vertical | 1 | HECS
18 | J2 | FanPinHeader_1x03_P2.54mm_Vertical | 1 | CASEFAN1
19 | J3 | FanPinHeader_1x03_P2.54mm_Vertical | 1 | CASEFAN2
20 | J12,J13 | Molex_KK-254_AE-6410-02A_1x02_P2.54mm_Vertical | 2 | NTC1
21 | J15 | PinSocket_2x03_P2.54mm_Vertical | 1 | ICSP
22 | L1 | Murata_DFE252012P_Inductor | 1 | 1uH
23 | L2 | PA2607 | 1 | 0.15uH
24 | Q1,Q2,Q3,Q4 | TO-252-2 | 4 | Q_NMOS_GDS
25 | R1 | R_0603_1608Metric | 1 | R_US
26 | R2,R3,R4,R7,R8,R21 | R_0603_1608Metric | 6 | 10k
27 | R5,R6,R19,R20 | R_0603_1608Metric | 4 | 1k
28 | R17,R23 | R_2512_6332Metric | 2 | 1Ω
29 | R18 | R_0603_1608Metric | 1 | 6.8k
30 | R24,R25 | R_2512_6332Metric | 2 | 0.02
31 | R26,R27 | R_0603_1608Metric | 2 | 10
32 | U1 | SOIC-8_3.9x4.9mm_P1.27mm | 1 | MCP2551-I-SN
33 | U3 | TQFP-32_7x7mm_P0.8mm | 1 | ATmega328P-AU
34 | U7 | Converter_DCDC_RECOM_R-78E-0.5_THT | 1 | R-78E5.0-0.5
35 | U8 | SOIC-8_3.9x4.9mm_P1.27mm | 1 | INA219
36 | J4 | Molex_KK-254_AE-6410-05A_1x05_P2.54mm_Vertical | 1 | Bender-LV
37 | F1 | Fuseholder_Cylinder-5x20mm_Schurter_0031_8201_Horizontal_Open_3d | 1 | 2A
38 | U6 | SMDIP-4_W9.53mm | 1 | LTV-817S
39 | RN1 | R_Array_Convex_4x0603 | 1 | 1k
40 | RN2 | R_Array_Convex_4x0603 | 1 | 10k
41 | C1 | CP_Radial_D10.0mm_P5.00mm | 1 | 470uF
42 | J5 | PhoenixContact_MCV_1,5_2-G-5.08_1x02_P5.08mm_Vertical | 1 | BLINKY
43 | J7 | TE_MATE-N-LOK_1-770870-x_1x03_P4.14mm_Vertical | 1 | HV-
44 | J8 | TE_MATE-N-LOK_1-770870-x_1x03_P4.14mm_Vertical | 1 | HV+
45 | Y1 | Resonator_SMD_muRata_CSTxExxV-3Pin_3.0x1.1mm | 1 | 16MHz
46 | U2 | SOIC-18W_7.5x11.6mm_P1.27mm | 1 | MCP2515-xSO

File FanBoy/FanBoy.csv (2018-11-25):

Id | Designator | Package | Quantity | Designation | Supplier and ref
1 | U2 | SOIC-8_3.9x4.9mm_P1.27mm | 1 | MCP2551-I-SN
2 | REF**,REF**,REF**,REF** | MountingHole_3.2mm_M3 | 4 | MountingHole_3.2mm_M3
3 | U4 | TQFP-32_7x7mm_P0.8mm | 1 | ATmega328P-AU
4 | J3 | PinSocket_2x03_P2.54mm_Vertical | 1 | Conn_02x03_Odd_Even
5 | C11,C10,C12,C13 | CP_Radial_D10.0mm_P5.00mm | 4 | C
6 | C1,C4 | C_0603_1608Metric | 2 | 10uF
7 | C2,C3,C5,C8,C9 | C_0603_1608Metric | 5 | 0.1uF
8 | C6,C7 | C_0603_1608Metric | 2 | 22pF
9 | D5,D6 | LED_0603_1608Metric | 2 | LED
10 | J1 | RJ45_Amphenol_54602-x08_Horizontal | 1 | RJ45
11 | R1,R2,R13 | R_0603_1608Metric | 3 | 10k
12 | R3,R4,R5,R6,R7,R8,R9,R10 | R_0603_1608Metric | 8 | R_US
13 | R11,R12 | R_0603_1608Metric | 2 | 1k
14 | U1 | Converter_DCDC_RECOM_R-78E-0.5_THT | 1 | R-78E5.0-0.5
15 | U3 | TSSOP-20_4.4x6.5mm_P0.65mm | 1 | MCP2515-IST
16 | Y1 | Crystal_HC49-U_Vertical | 1 | 8MHz
17 | Q1,Q2,Q3,Q4 | TO-252-2 | 4 | Q_NMOS_GDS
18 | D1,D2,D3,D4 | D_DO-41_SOD81_P10.16mm_Horizontal | 4 | D
19 | J2 | TerminalBlock_MetzConnect_Type067_RT01902HDWC_1x02_P10.00mm_Horizontal | 1 | Screw_Terminal_01x02
20 | J4 | TerminalBlock_Phoenix_MKDS-1,5-8_1x08_P5.00mm_Horizontal | 1 | Screw_Terminal_01x08
21 | G*** | logo | 1 | LOGO

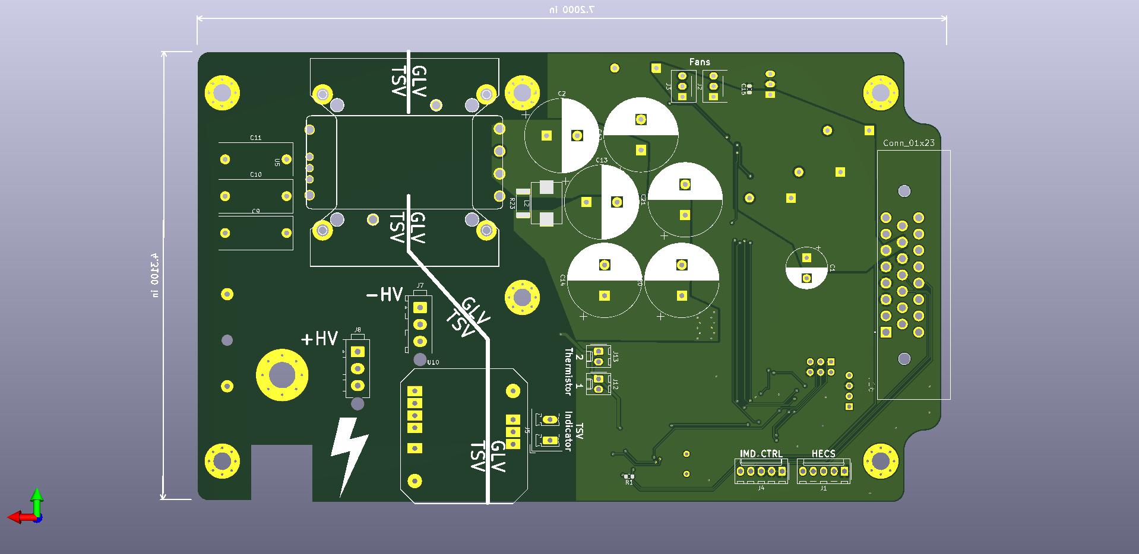
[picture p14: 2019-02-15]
interface-board-standoffs-biggerbox/board-images/back-no-parts.jpg

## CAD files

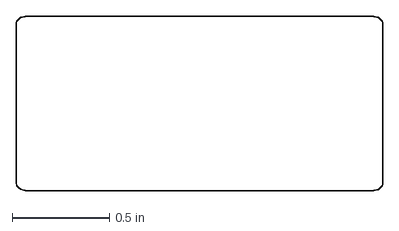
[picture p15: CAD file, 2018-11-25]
DC_DCBoard/TESTboard/DCM_projection.dxf
1.89 x 0.898 in

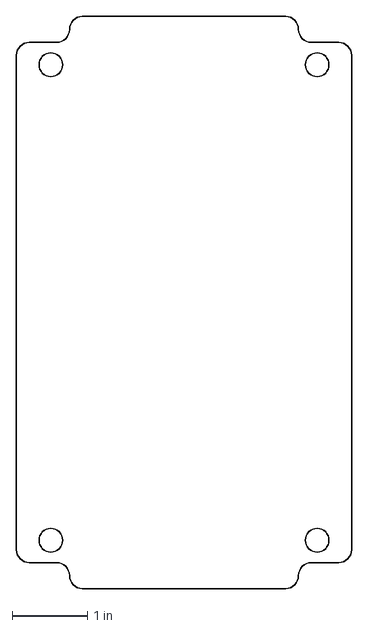
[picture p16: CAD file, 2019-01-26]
interface-board-standoffs-biggerbox/insideBoxProjection.dxf
4.46 x 7.61 in

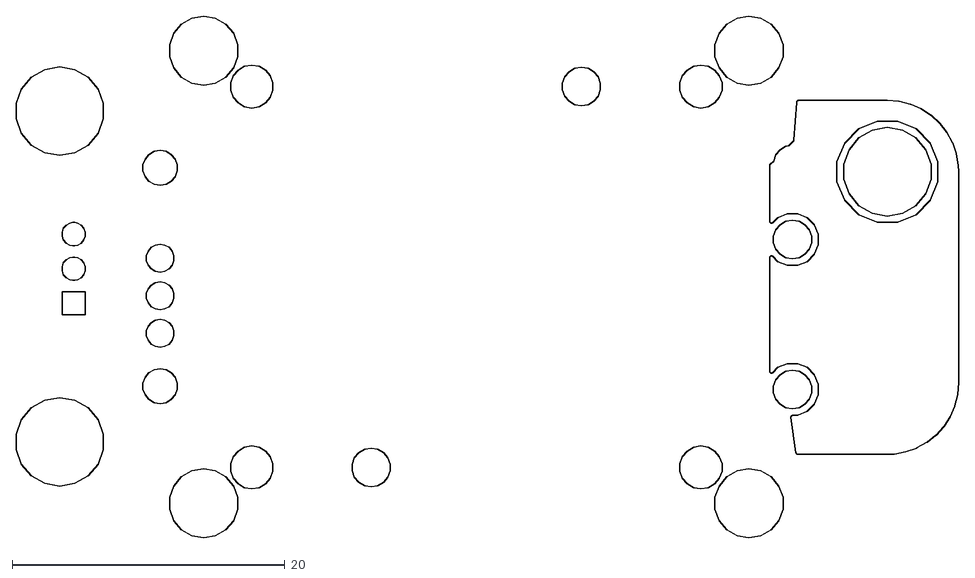
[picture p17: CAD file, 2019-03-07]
vicor-socket/DXFS/vicor-socket-B.Cu.dxf
69.1 x 38.3

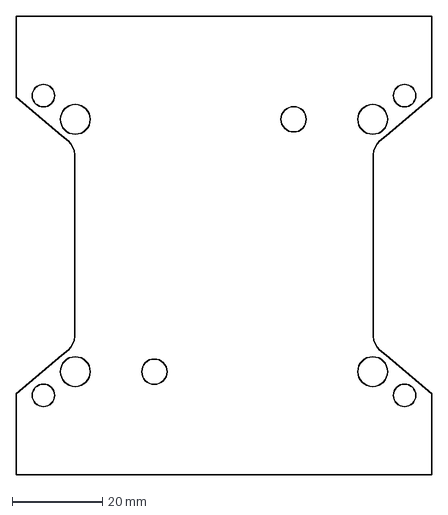
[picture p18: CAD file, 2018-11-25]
DC_DCBoard/TESTboard/U4SP6G.DXF
92.0 x 101.6 mm

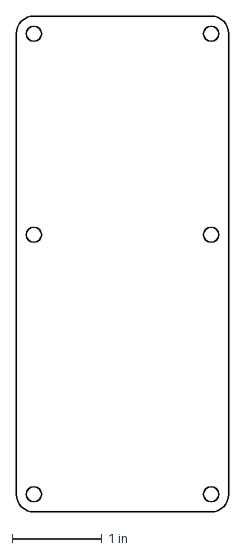
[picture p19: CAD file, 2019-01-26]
interface-board-standoffs-biggerbox/benderProjection.dxf
2.36 x 5.51 in

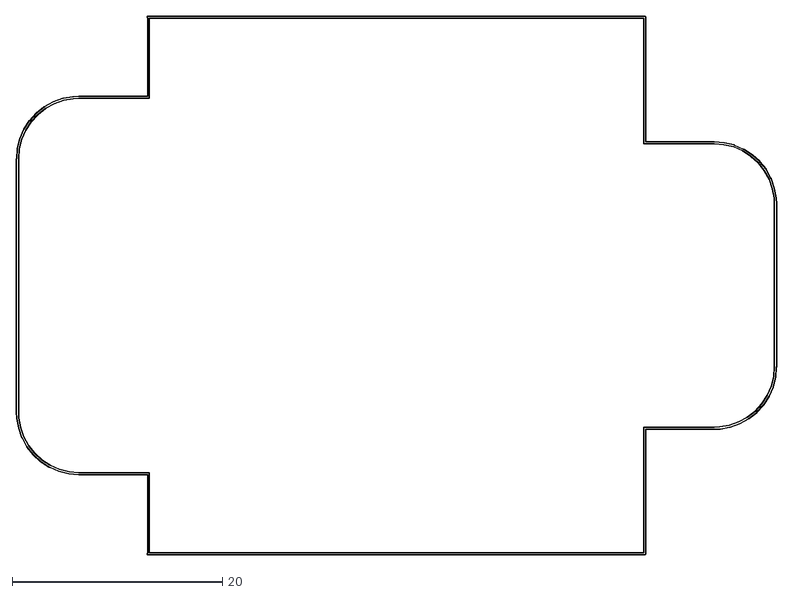
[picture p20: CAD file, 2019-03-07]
vicor-socket/DXFS/vicor-socket-Edge.Cuts.dxf
72.3 x 51.3

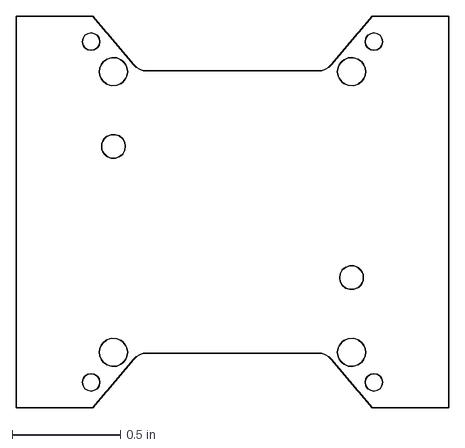
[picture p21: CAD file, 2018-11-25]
DC_DCBoard/TESTboard/vicor_40098_footprint_silkscreen.dxf
2.00 x 1.81 in

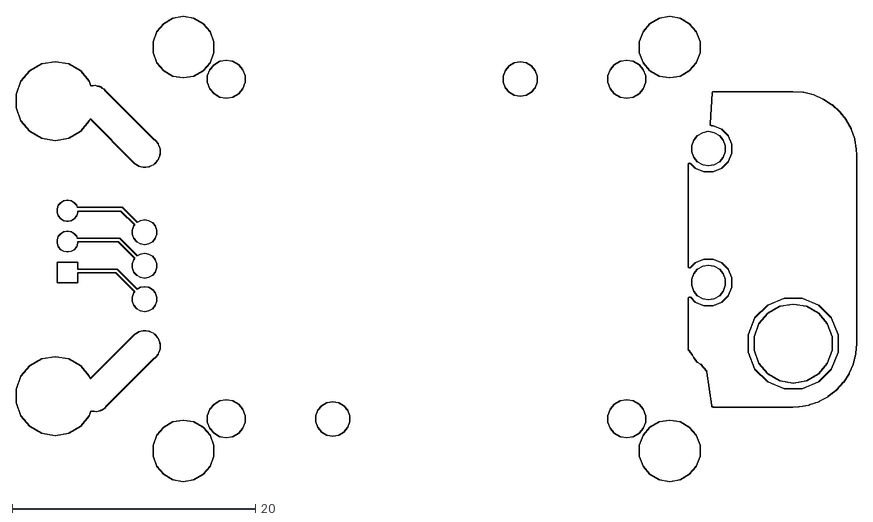
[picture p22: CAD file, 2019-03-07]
vicor-socket/DXFS/vicor-socket-F.Cu.dxf
69.1 x 38.3

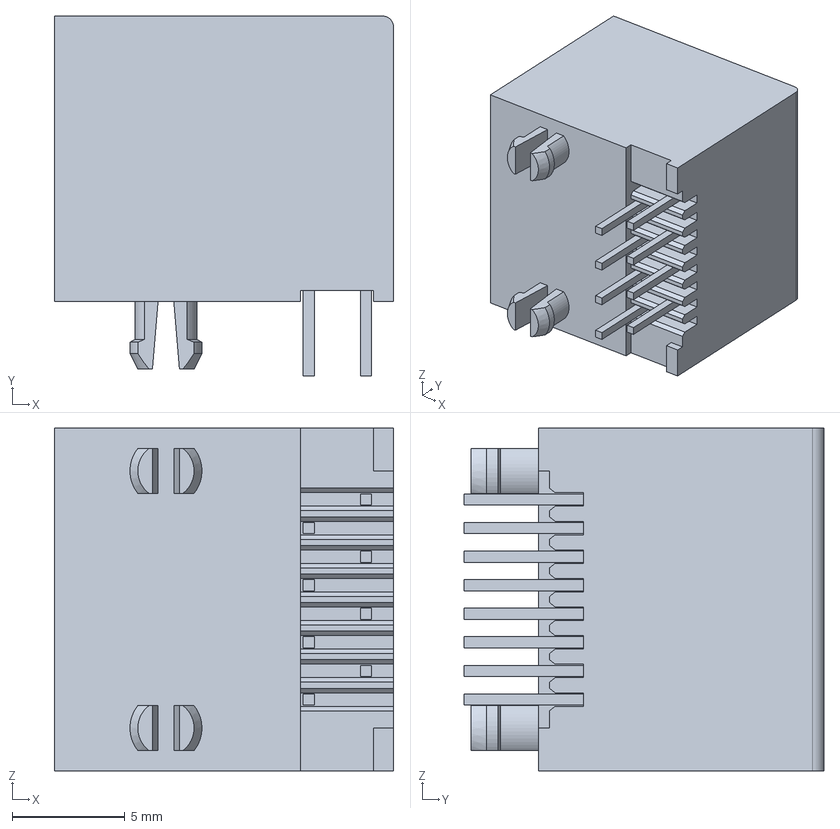
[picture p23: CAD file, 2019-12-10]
3d_models/955032884.stp
15.1 x 16.0 x 15.2 mm

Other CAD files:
vicor-socket/DXFS/vicor-socket-B.Mask.dxf
vicor-socket/DXFS/vicor-socket-B.Paste.dxf
vicor-socket/DXFS/vicor-socket-B.SilkS.dxf
vicor-socket/DXFS/vicor-socket-F.Mask.dxf
vicor-socket/DXFS/vicor-socket-F.Paste.dxf
vicor-socket/DXFS/vicor-socket-F.SilkS.dxf

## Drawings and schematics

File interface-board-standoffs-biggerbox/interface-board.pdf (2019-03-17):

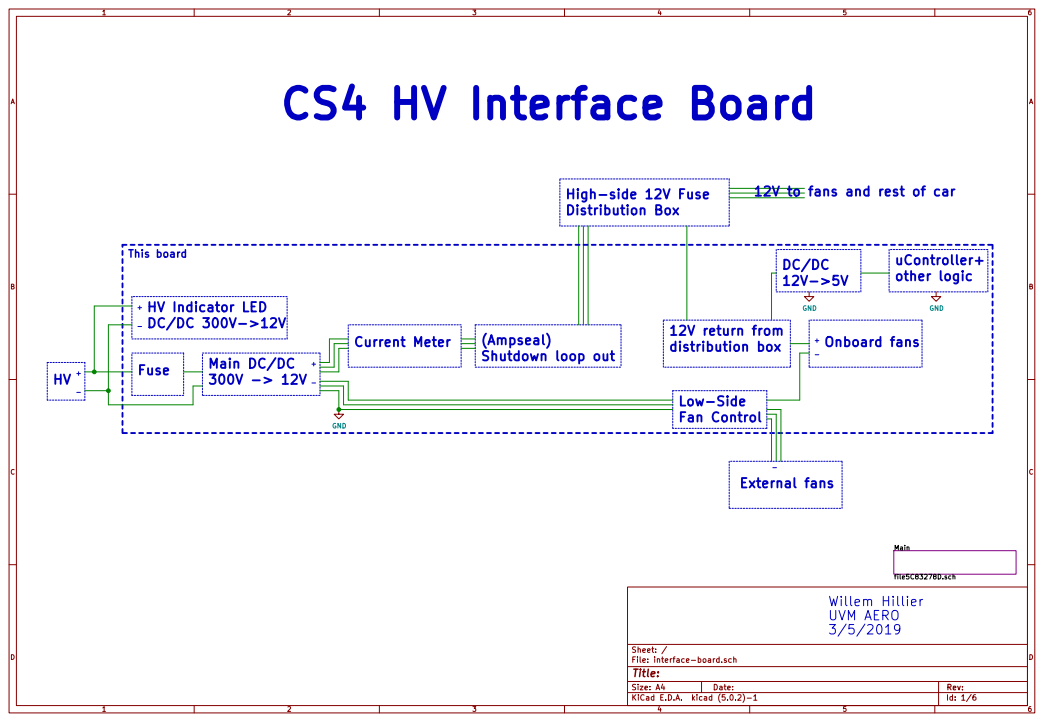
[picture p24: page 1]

file5C83278D.sch CS4 HV Interface Board

distribution box

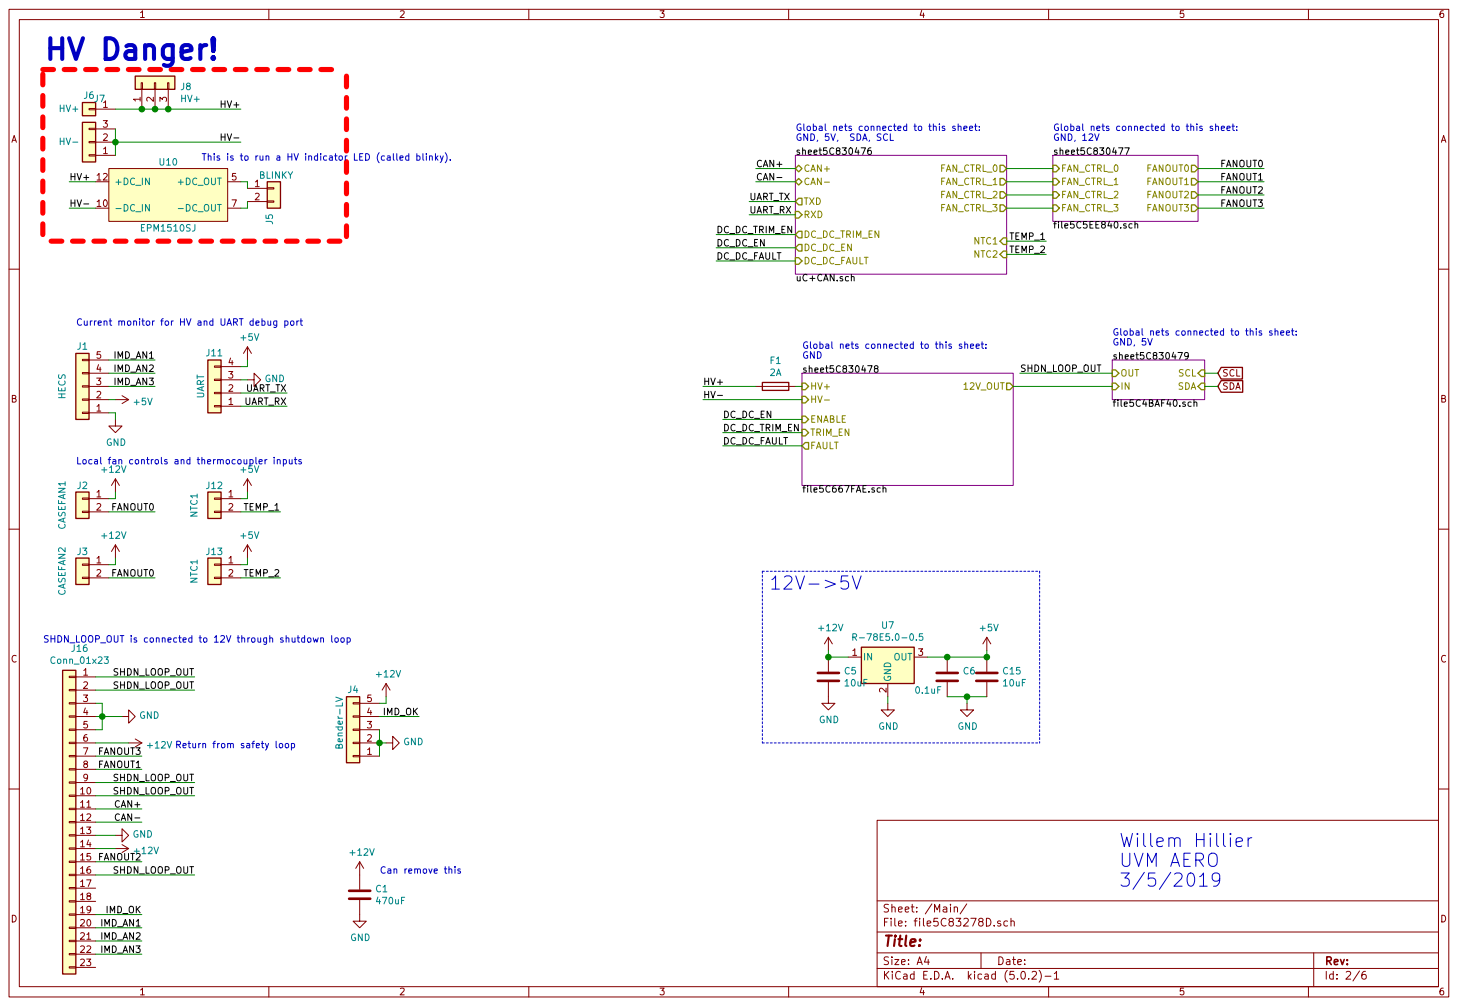
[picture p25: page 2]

This is to run a HV indicator LED (called blinky).

Current monitor for HV and UART debug port

Local fan controls and thermocoupler inputs

Id: 2/6 Title: File: file5C83278D.sch Sheet: /Main/

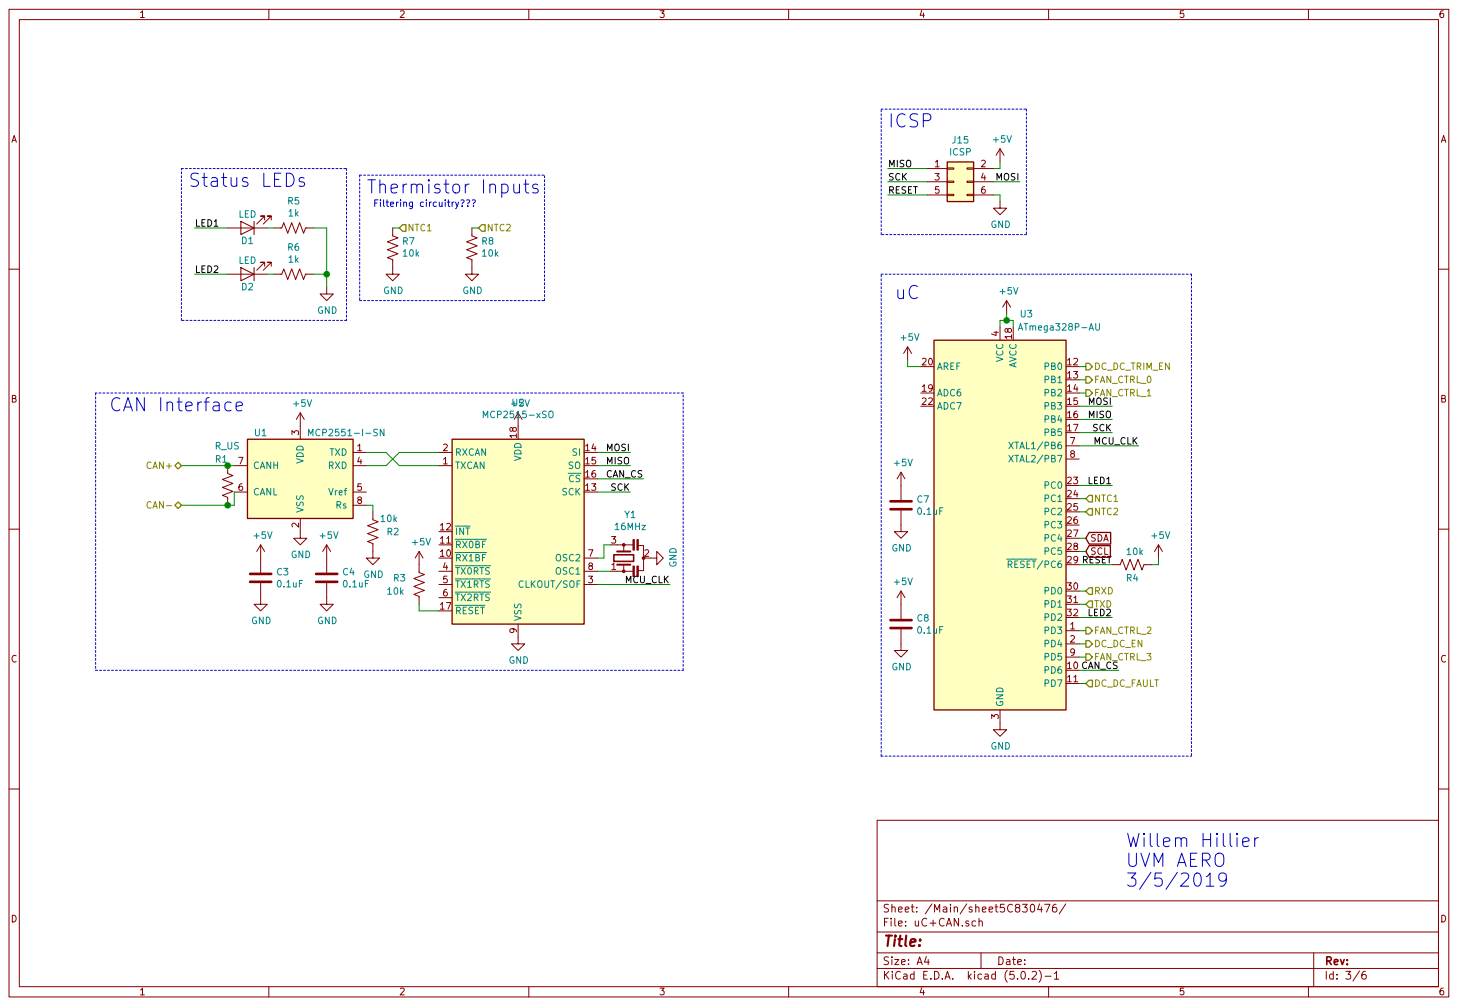
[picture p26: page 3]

3 RXD 4 Vref 5 CANL 6 CANH 7 Rs 8 U1 MCP2551-I-SN

Id: 3/6 Title: File: uC+CAN.sch Sheet: /Main/sheet5C830476/

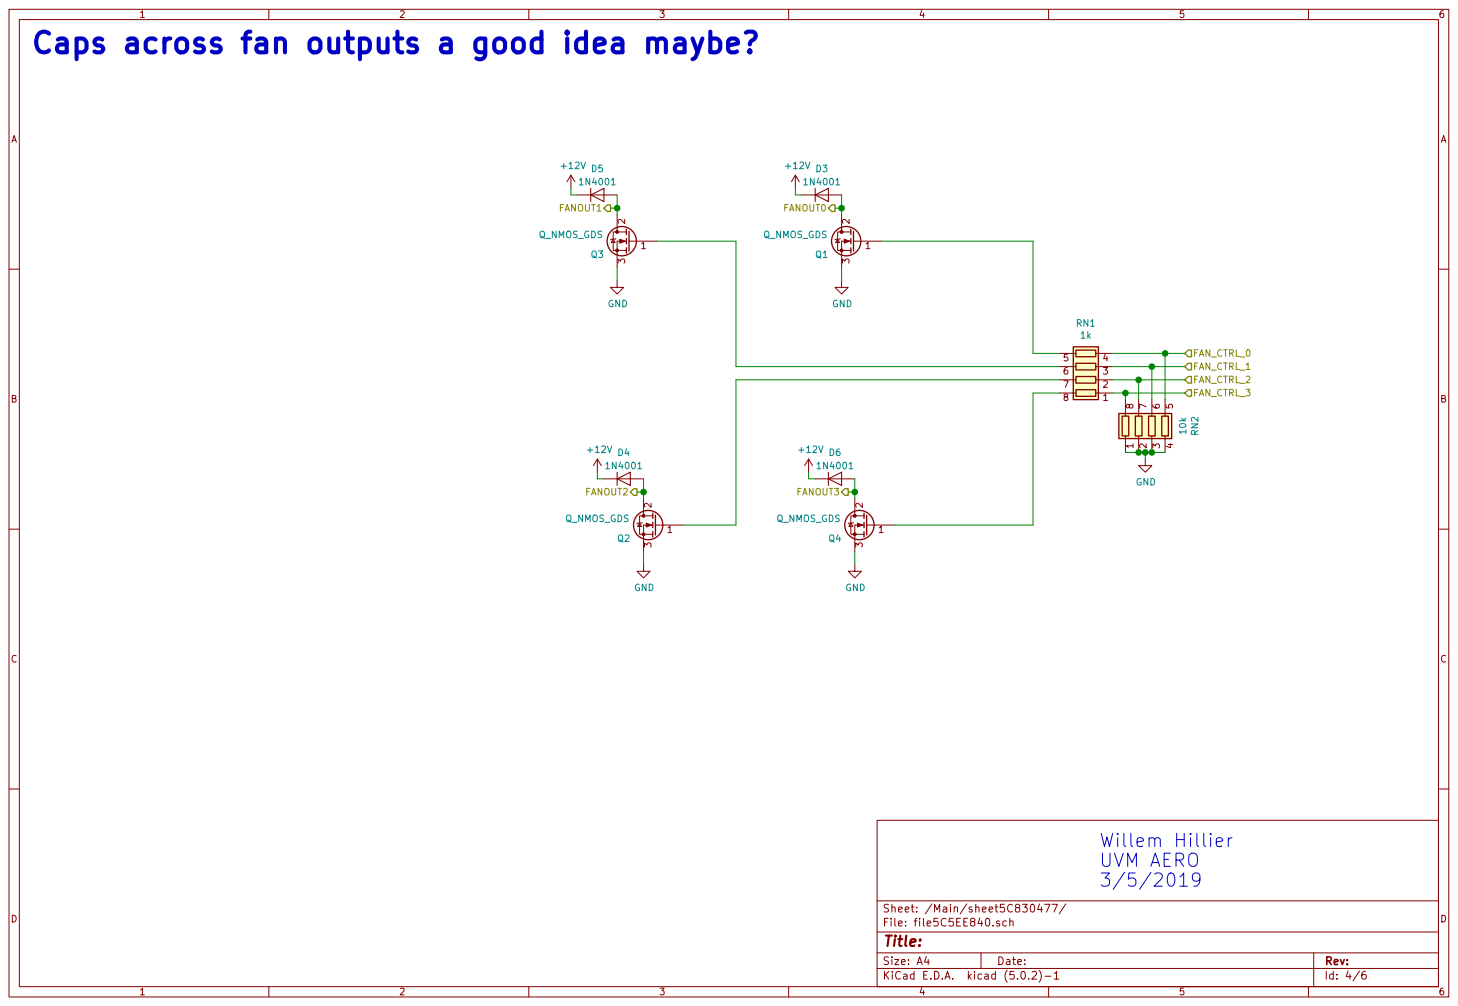
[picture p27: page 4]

Id: 4/6 Title: File: file5C5EE840.sch Sheet: /Main/sheet5C830477/

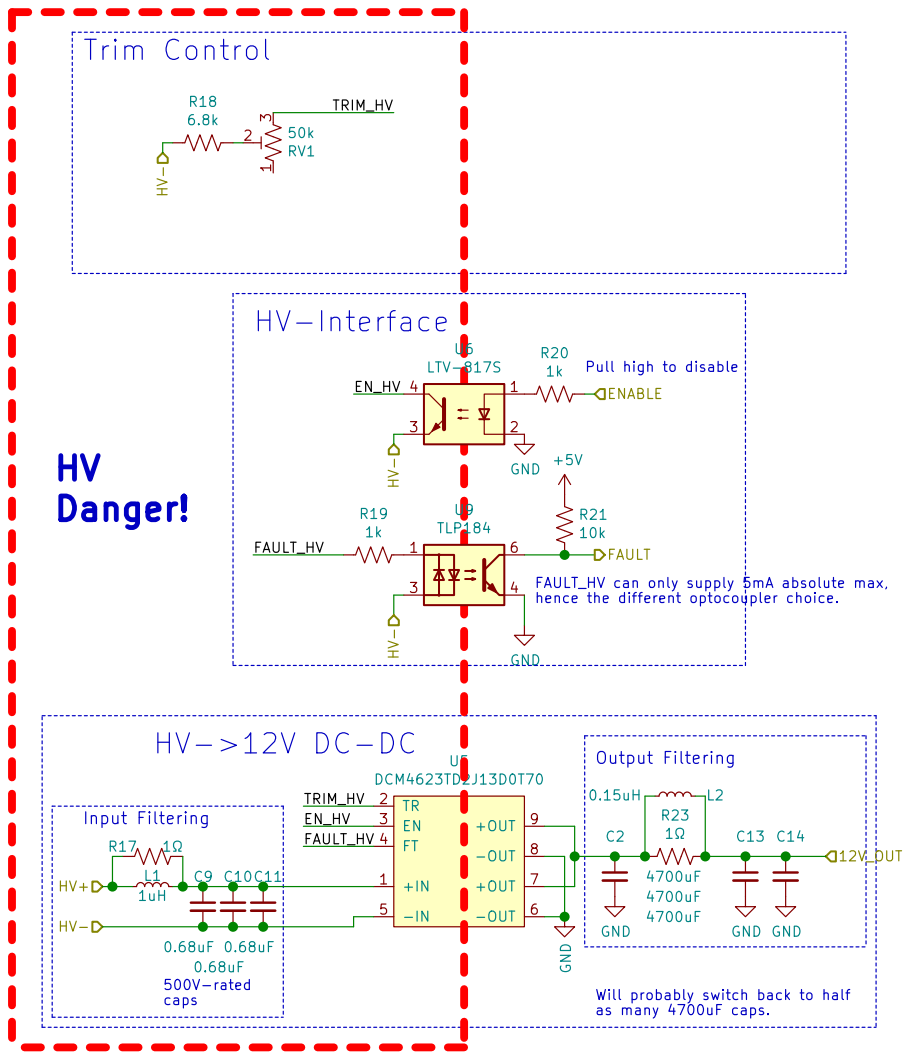
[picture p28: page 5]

Pull high to disable R20

FAULT_HV can only supply 5mA absolute max,
hence the different optocoupler choice.

Will probably switch back to half
as many 4700uF caps.

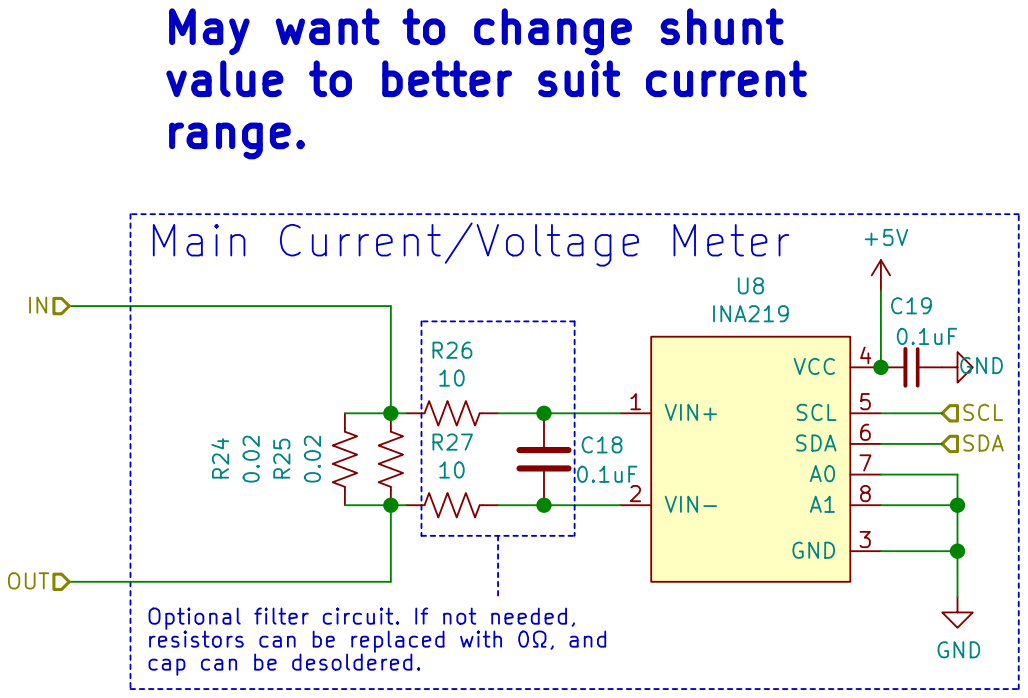
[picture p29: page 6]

INA219 May want to change shunt
value to better suit current

Main Current/Voltage Meter R26

Optional filter circuit. If not needed,
resistors can be replaced with 0, and

Id: 6/6 Title: File: file5C4BAF40.sch Sheet: /Main/sheet5C830479/

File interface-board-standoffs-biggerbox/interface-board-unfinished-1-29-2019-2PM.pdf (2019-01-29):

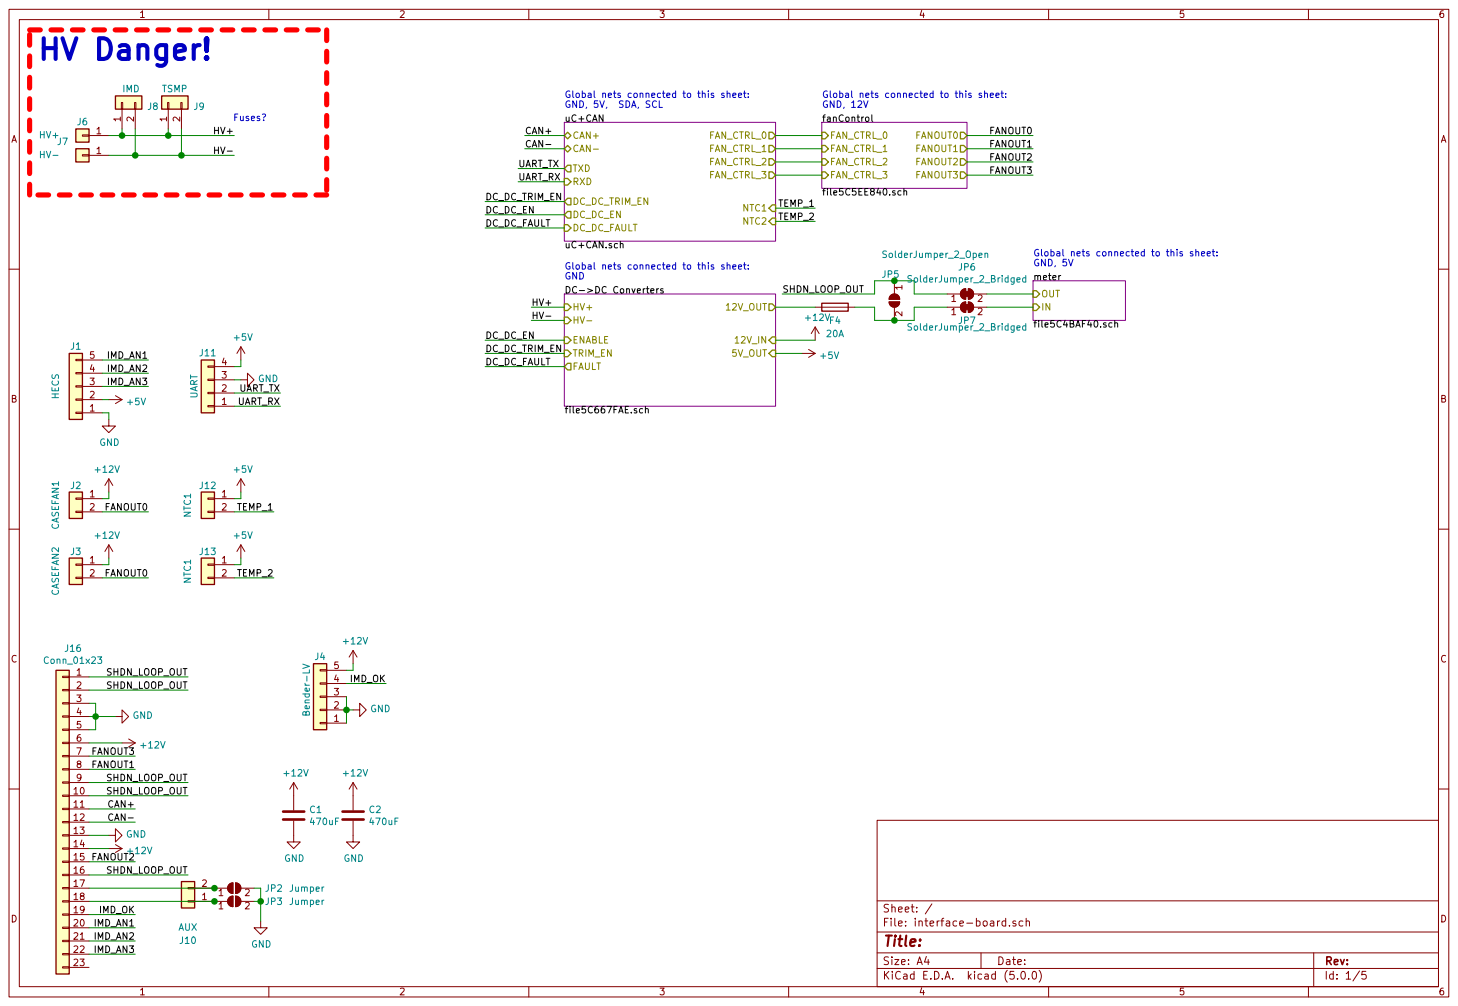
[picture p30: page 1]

Id: 1/5 Title: File: interface-board.sch Sheet: /

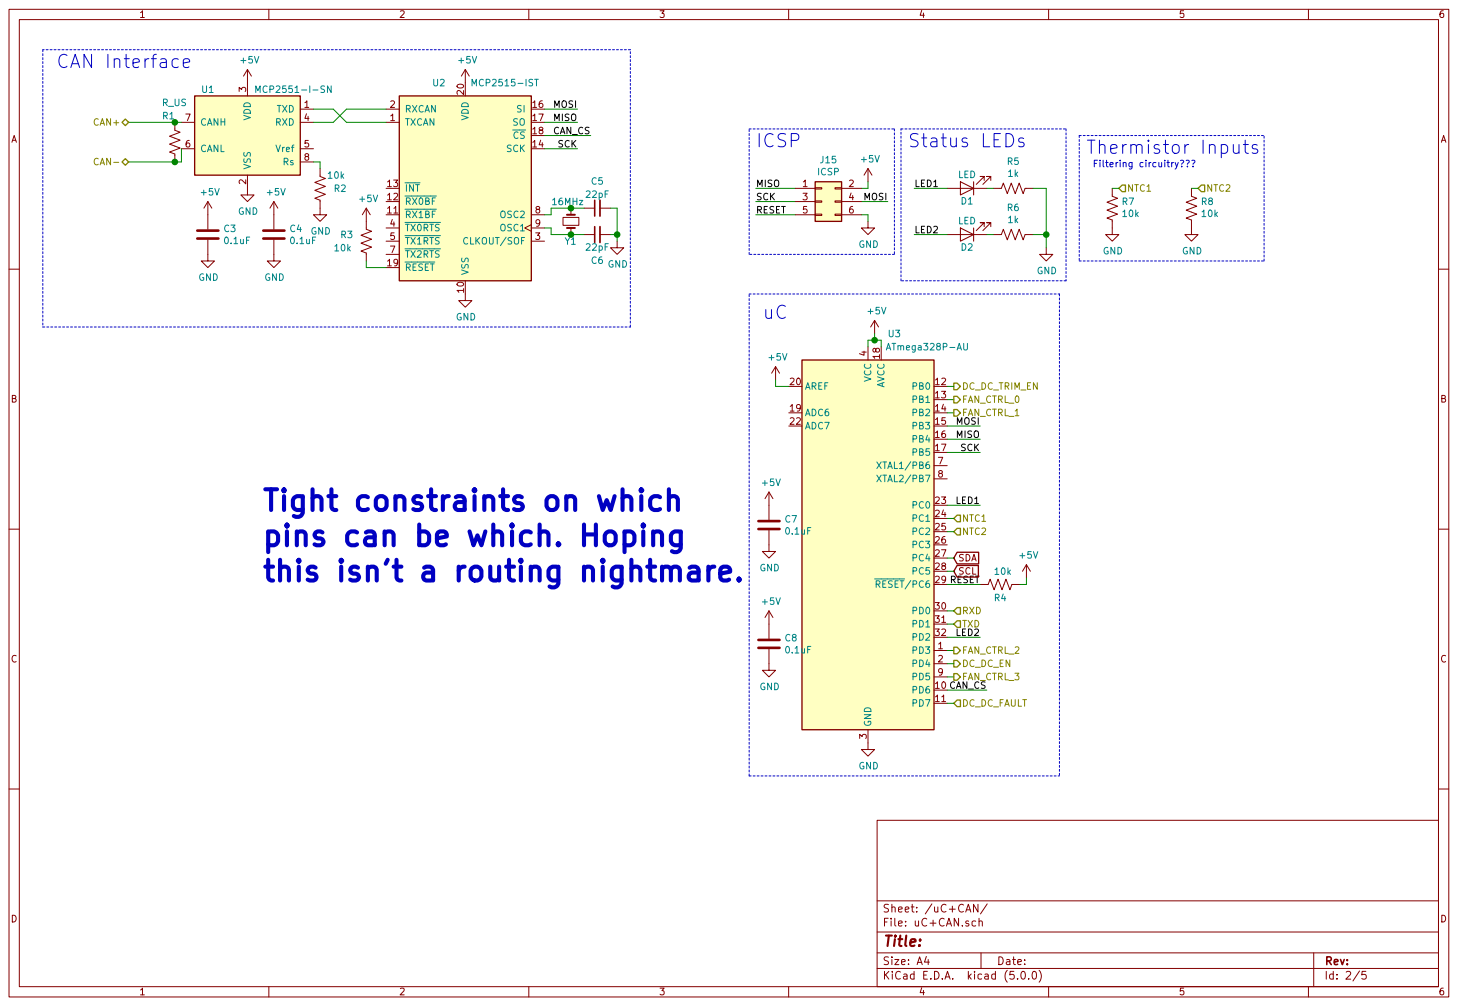
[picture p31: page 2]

3 RXD 4 Vref 5 CANL 6 CANH 7 Rs 8 U1 MCP2551-I-SN

TXD Tight constraints on which
pins can be which. Hoping
this isn't a routing nightmare.

Id: 2/5 Title: File: uC+CAN.sch Sheet: /uC+CAN/

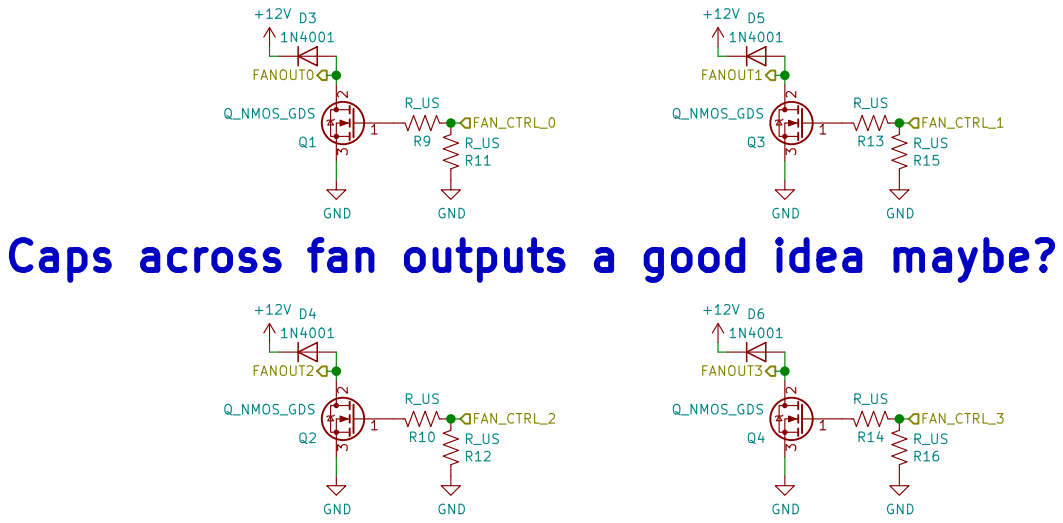
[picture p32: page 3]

Id: 3/5 Title: File: file5C5EE840.sch Sheet: /fanControl/

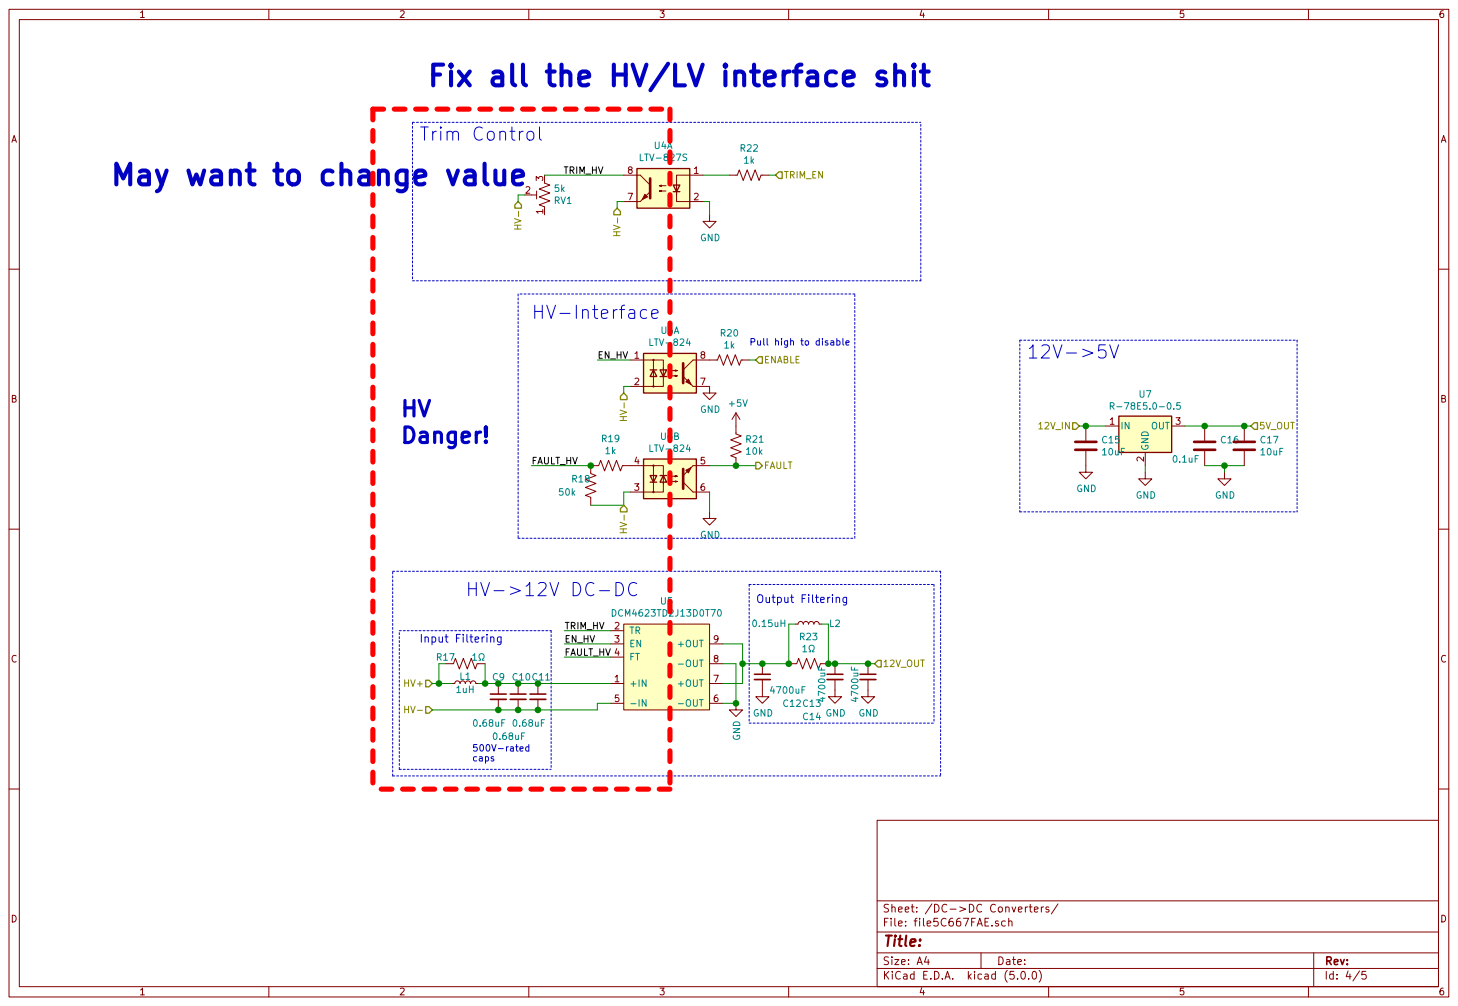
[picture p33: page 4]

5V_OUT Fix all the HV/LV interface shit
TRIM_HV HV->12V DC-DC

8 U4A LTV-827S

Pull high to disable R20

-IN 5 | 6 +OUT 7

-OUT

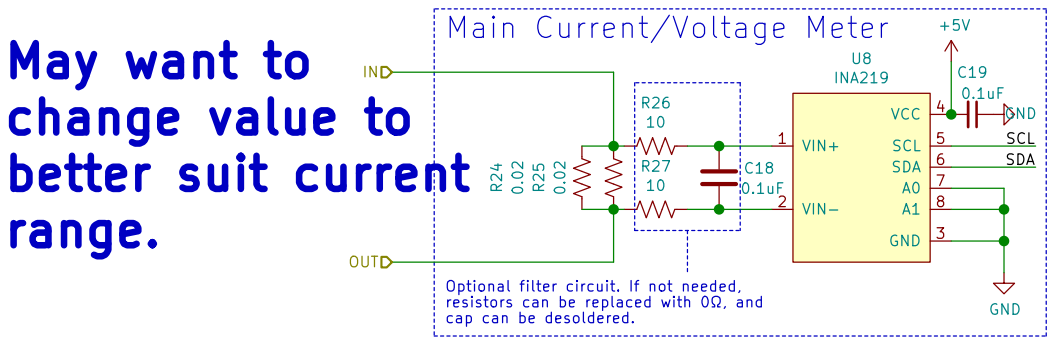
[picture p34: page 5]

Main Current/Voltage Meter R26

Optional filter circuit. If not needed,
resistors can be replaced with 0, and

Id: 5/5 Title: File: file5C4BAF40.sch Sheet: /meter/

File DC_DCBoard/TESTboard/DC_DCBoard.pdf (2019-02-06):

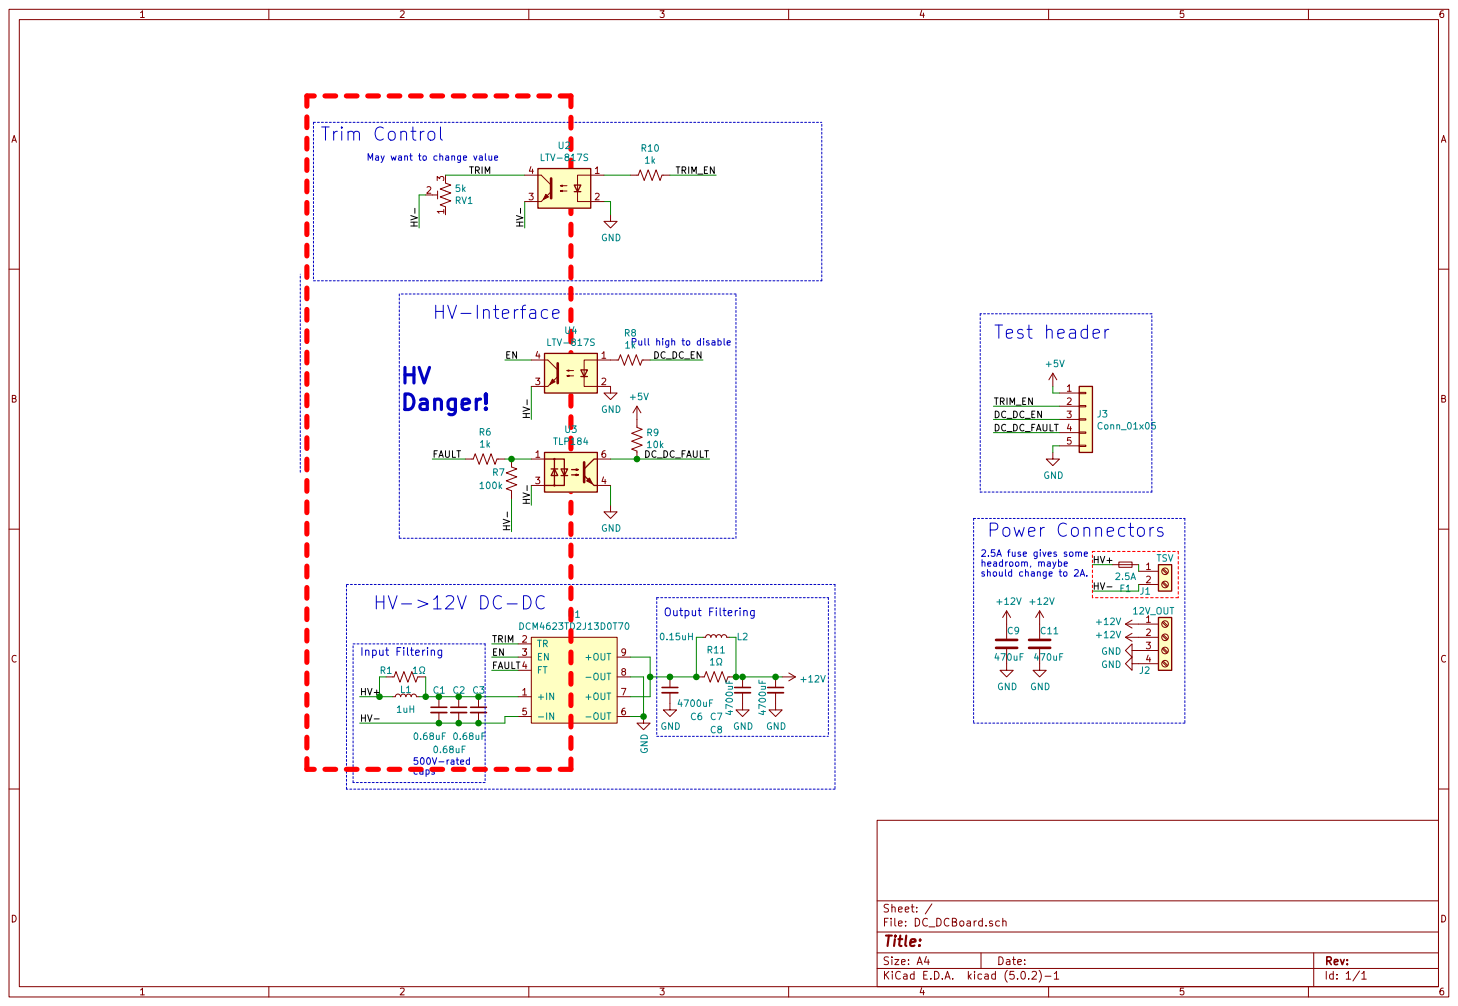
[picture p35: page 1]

2.5A HV+ HV- May want to change value

Pull high to disable R8

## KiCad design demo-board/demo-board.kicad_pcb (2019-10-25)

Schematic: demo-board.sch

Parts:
C1: 0.1U; C_0603_1608Metric_Pad1.05x0.95mm_HandSolder
C2: 10U; C_0603_1608Metric_Pad1.05x0.95mm_HandSolder
D1, D2, D3, D4, D5, D6, D7, D8: WS2812B; LED_WS2812B_PLCC4_5.0x5.0mm_P3.2mm
J1: USB_B_Micro; USB_Micro-B_Molex-105017-0001
J2: Conn_02x03_Odd_Even; PinHeader_2x03_P2.54mm_Vertical
JP1, JP2, JP3, JP4, JP5, JP6, JP7, JP8: Jumper_2_Open; SolderJumper-2_P1.3mm_Open_RoundedPad1.0x1.5mm
R1: 1OK; R_0603_1608Metric_Pad1.05x0.95mm_HandSolder
U1: ATtiny85-20SU; SOIJ-8_5.3x5.3mm_P1.27mm

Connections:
+5V: C1.1, C2.1, D1.1 (VDD), D2.1 (VDD), D3.1 (VDD), D4.1 (VDD), D5.1 (VDD), D6.1 (VDD), D7.1 (VDD), D8.1 (VDD), J1.1 (VBUS), J2.2, R1.1, U1.8 (VCC)
/MISO: J2.1, U1.6 (PB1)
/MOSI: J2.4, U1.5 (AREF/PB0)
/RST: J2.5, R1.2, U1.1 (~RESET~/PB5)
/SCK: J2.3, U1.7 (PB2)
GND: C1.2, C2.2, D1.3 (VSS), D2.3 (VSS), D3.3 (VSS), D4.3 (VSS), D5.3 (VSS), D6.3 (VSS), D7.3 (VSS), D8.3 (VSS), J1.5 (GND), J1.6 (Shield), J2.6, U1.4 (GND)
unnamed: D1.2 (DOUT), D3.4 (DIN), JP1.2 (B), JP3.1 (A)
unnamed: D1.4 (DIN), JP1.1 (A), U1.2 (XTAL1/PB3)
unnamed: D2.2 (DOUT), D4.4 (DIN), JP2.2 (B), JP4.1 (A)
unnamed: D2.4 (DIN), D7.2 (DOUT), JP2.1 (A), JP7.2 (B)
unnamed: D3.2 (DOUT), D5.4 (DIN), JP3.2 (B), JP5.1 (A)
unnamed: D4.2 (DOUT), D6.4 (DIN), JP4.2 (B), JP6.1 (A)
unnamed: D5.2 (DOUT), D7.4 (DIN), JP5.2 (B), JP7.1 (A)
unnamed: D6.2 (DOUT), D8.4 (DIN), JP6.2 (B), JP8.1 (A)
unnamed: D8.2 (DOUT), JP8.2 (B)

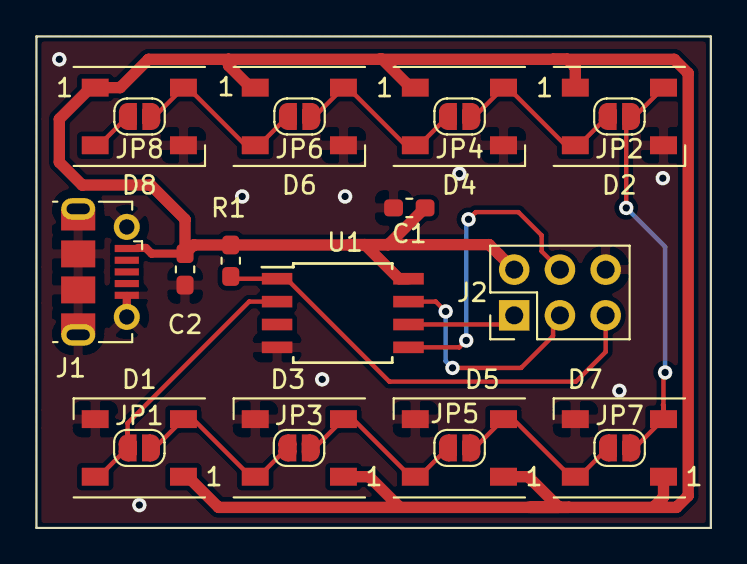
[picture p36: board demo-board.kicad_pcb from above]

Board: 2 copper layers, 37.5 x 27.3 mm, 22 parts (0 on the bottom side), 15 nets.

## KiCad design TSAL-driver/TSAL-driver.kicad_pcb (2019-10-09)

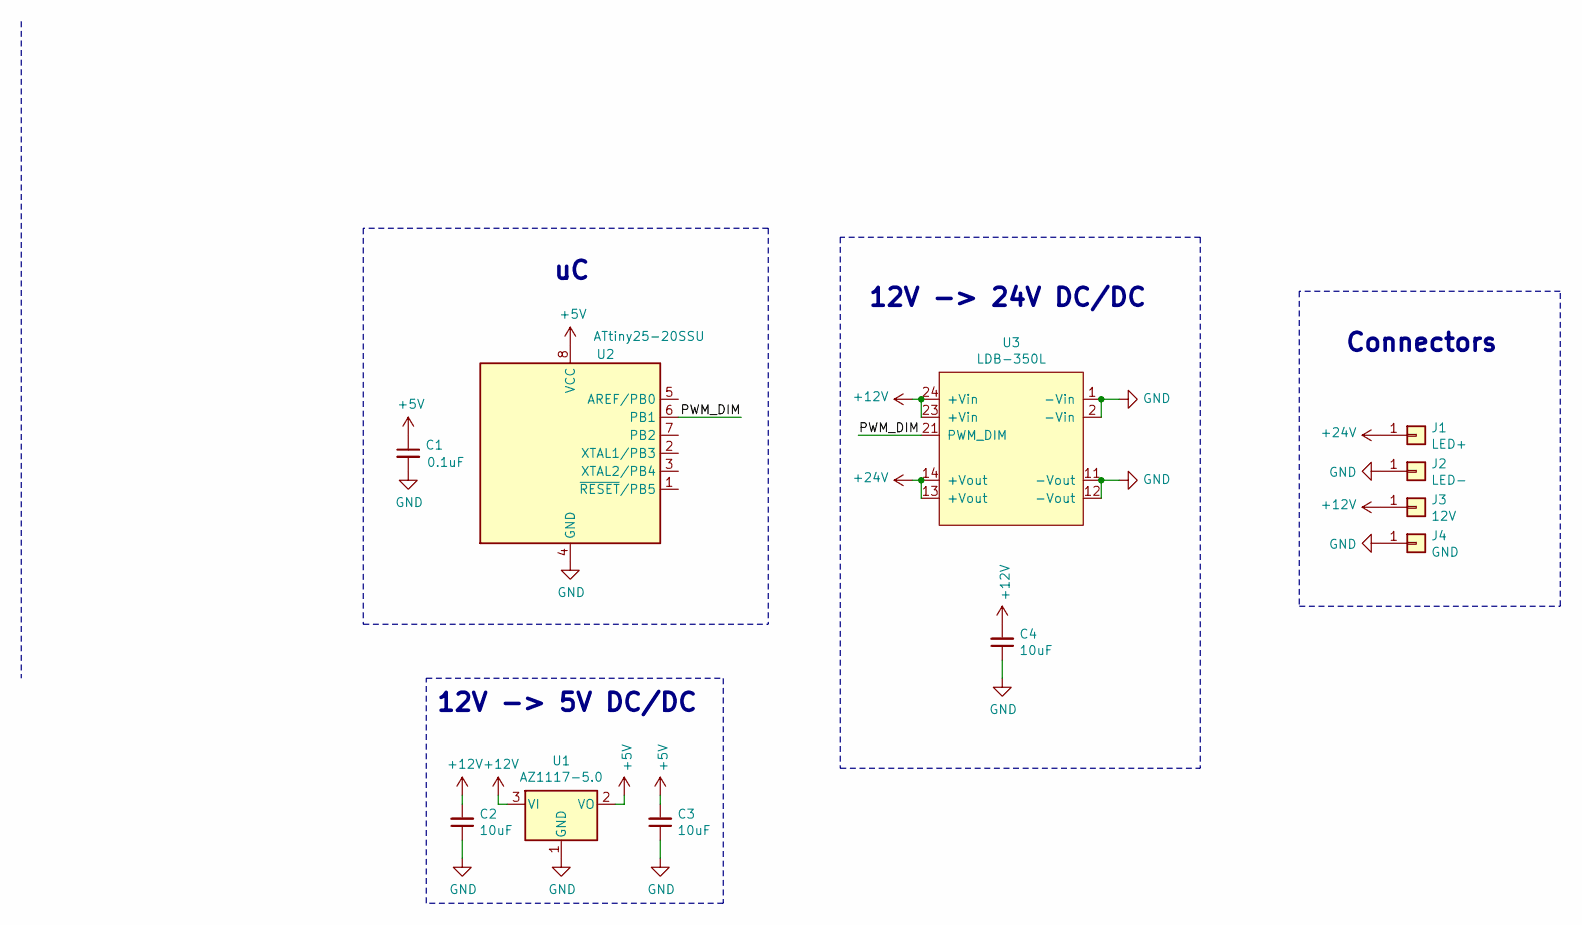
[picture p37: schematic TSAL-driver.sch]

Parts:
C1: 0.1uF; C_0603_1608Metric
C2, C3, C4: 10uF; C_0603_1608Metric
J1: LED+; TE_1217861-1
J2: LED-; TE_1217861-1
J3: 12V; TE_1217861-1
J4: GND; TE_1217861-1
U1: AZ1117-5.0; SOT-223-3_TabPin2
U2: ATtiny25-20SSU; SOIC-8_3.9x4.9mm_P1.27mm
U3: LDB-350L; LDB-_L

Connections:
+5V: C1.1, C3.2, U1.2 (VO), U2.8 (VCC)
+12V: C2.2, C4.2, J3.1, U1.3 (VI), U3.23 (+Vin), U3.24 (+Vin)
+24V: J1.1, U3.13 (+Vout), U3.14 (+Vout)
/PWM_DIM: U2.6 (PB1), U3.21 (PWM_DIM)
GND: C1.2, C2.1, C3.1, C4.1, J2.1, J4.1, U1.1 (GND), U2.4 (GND), U3.1 (-Vin), U3.2 (-Vin), U3.11 (-Vout), U3.12 (-Vout)

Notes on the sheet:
12V -> 24V DC/DC
Connectors
12V -> 5V DC/DC

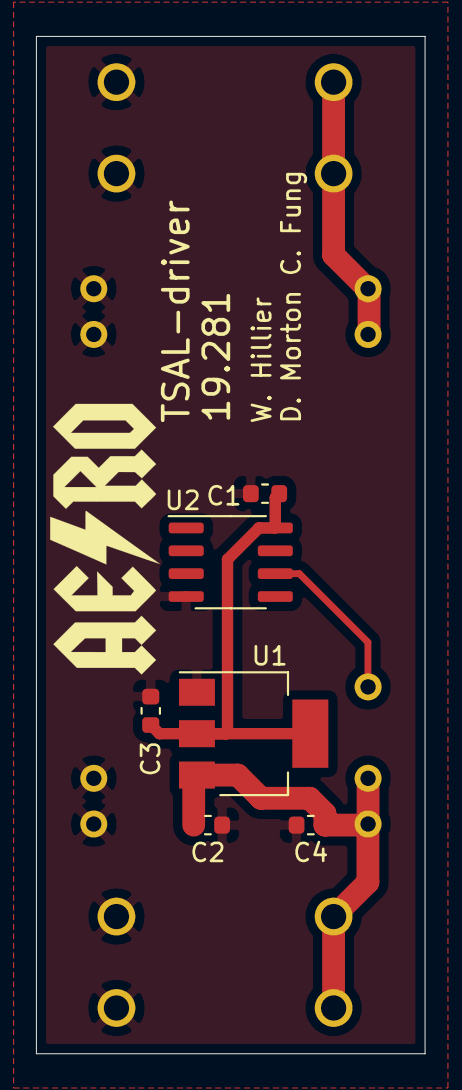
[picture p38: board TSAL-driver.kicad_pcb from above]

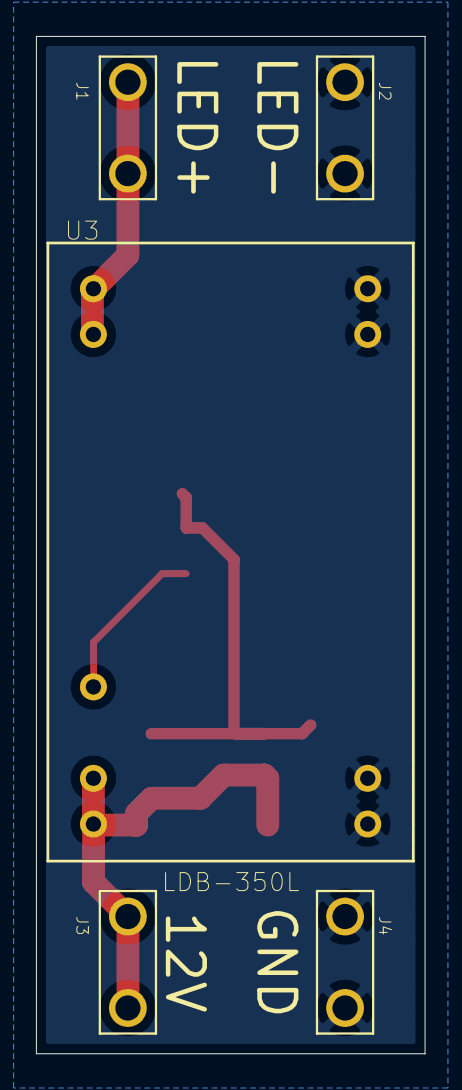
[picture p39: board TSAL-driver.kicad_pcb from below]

Board: 2 copper layers, 21.6 x 56.5 mm, 11 parts (5 on the bottom side), 5 nets.

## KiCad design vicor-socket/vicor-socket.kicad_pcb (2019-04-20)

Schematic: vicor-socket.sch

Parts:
J1: Interface; PinHeader_1x03_P2.54mm_Vertical
J2: HV+; MountingHole_3.2mm_M3_Pad_Via
J3: HV-; MountingHole_3.2mm_M3_Pad_Via
J4: 12V+; MountingHole_3.2mm_M3_Pad_Via
J5: 12V-; MountingHole_3.2mm_M3_Pad_Via
U1: DCM4623TD2J13D0T70-AEROParts; DCM4623TD2J13D0T70_w_landpattern

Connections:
unnamed: J1.1, U1.4 (FT)
unnamed: J1.2, U1.3 (EN)
unnamed: J1.3, U1.2 (TR)
unnamed: J2.1, U1.1 (+IN)
unnamed: J3.1, U1.5 (-IN)
unnamed: J4.1, U1.7 (+OUT), U1.9 (+OUT)
unnamed: J5.1, U1.6 (-OUT), U1.8 (-OUT)

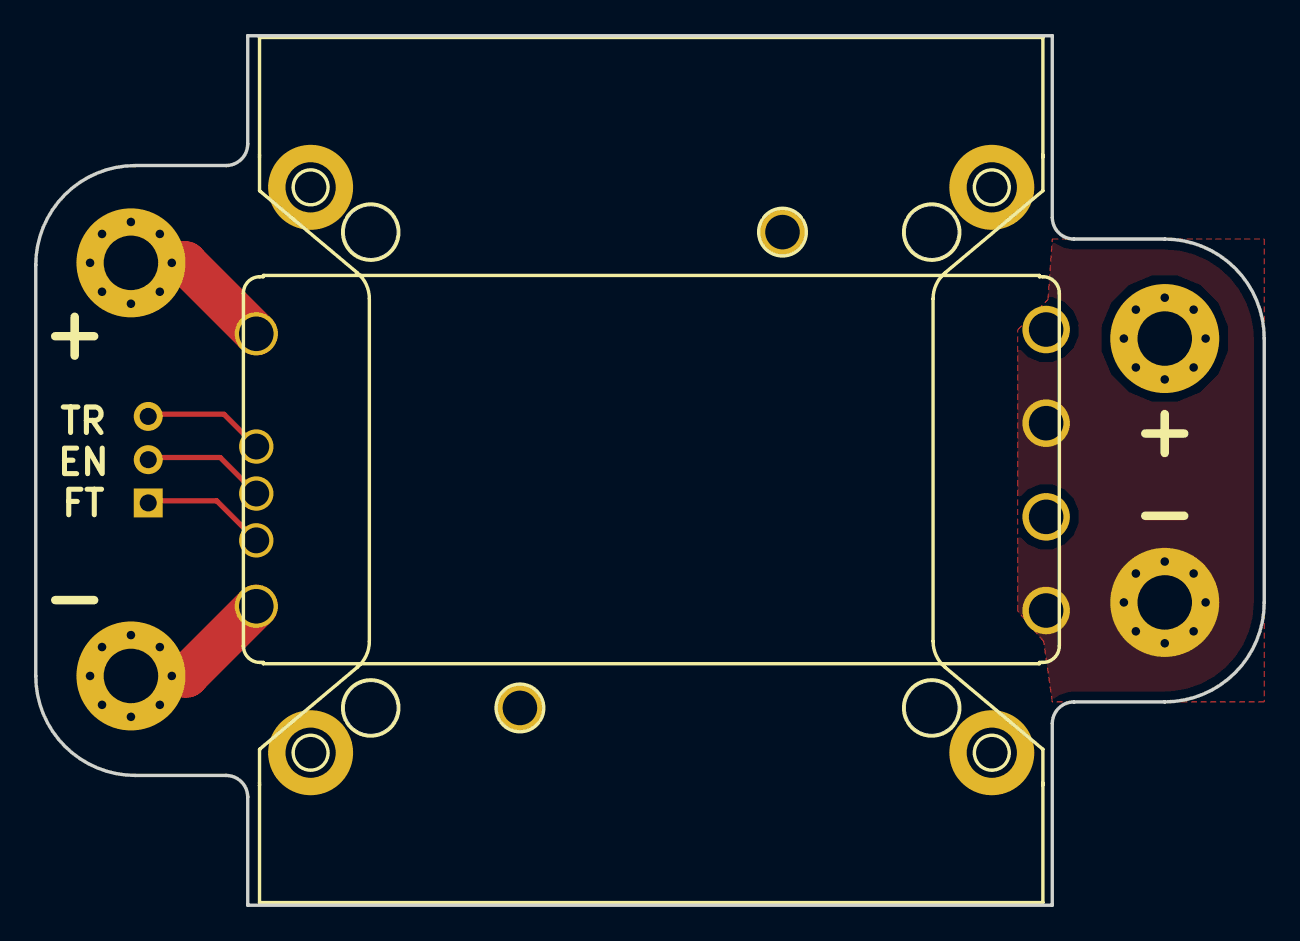
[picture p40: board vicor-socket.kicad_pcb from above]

Board: 2 copper layers, 72.1 x 51.1 mm, 6 parts (1 on the bottom side), 7 nets.

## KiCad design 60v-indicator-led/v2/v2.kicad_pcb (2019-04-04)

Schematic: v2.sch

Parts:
D1: RED_LED; LPA-C011301S-x LED 0805 LIGHT PIPE SINGLE VERT SMD
J1, J2: Conn_01x02; TE_MATE-N-LOK_1-770866-x_1x02_P4.14mm_Vertical
R1, R2, R3, R4, R5, R6, R7, R8, R9, R10: 1k; R_0805_2012Metric

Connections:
unnamed: D1.1 (K), R10.1
unnamed: D1.2 (A), R9.1
unnamed: J1.1, J1.2, R1.2
unnamed: J2.1, J2.2, R2.2
unnamed: R1.1, R3.2
unnamed: R2.1, R4.2
unnamed: R3.1, R5.2
unnamed: R4.1, R6.2
unnamed: R5.1, R7.2
unnamed: R6.1, R8.2
unnamed: R7.1, R9.2
unnamed: R8.1, R10.2

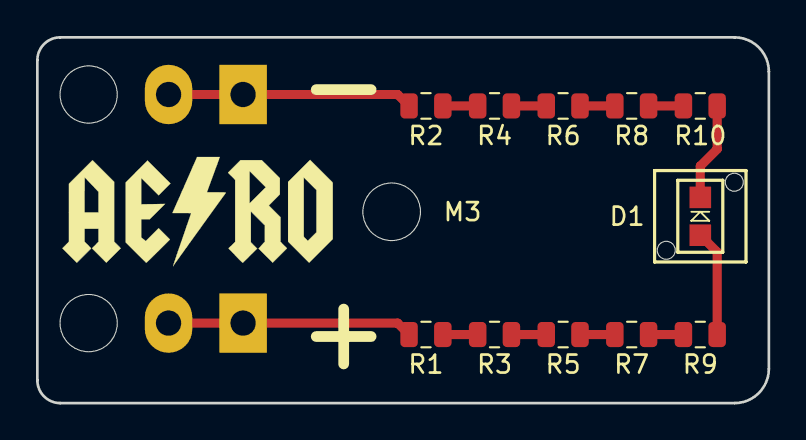
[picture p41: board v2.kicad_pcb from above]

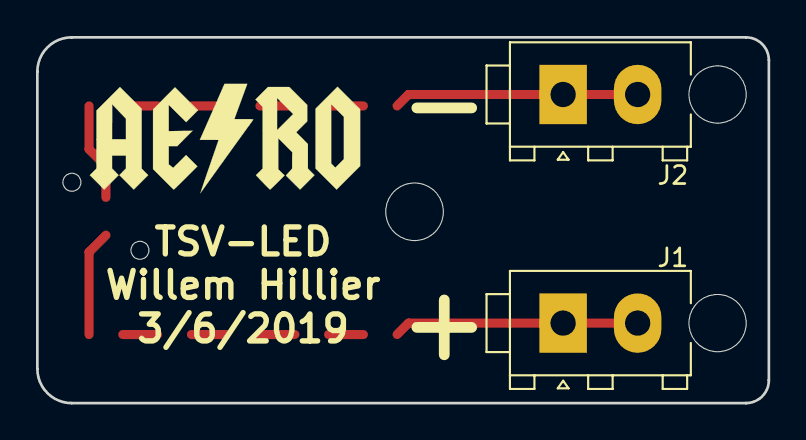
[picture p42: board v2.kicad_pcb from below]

Board: 2 copper layers, 40.6 x 20.3 mm, 14 parts (2 on the bottom side), 12 nets.

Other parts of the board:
M3: MountingHole_3.2mm_M3_DIN965

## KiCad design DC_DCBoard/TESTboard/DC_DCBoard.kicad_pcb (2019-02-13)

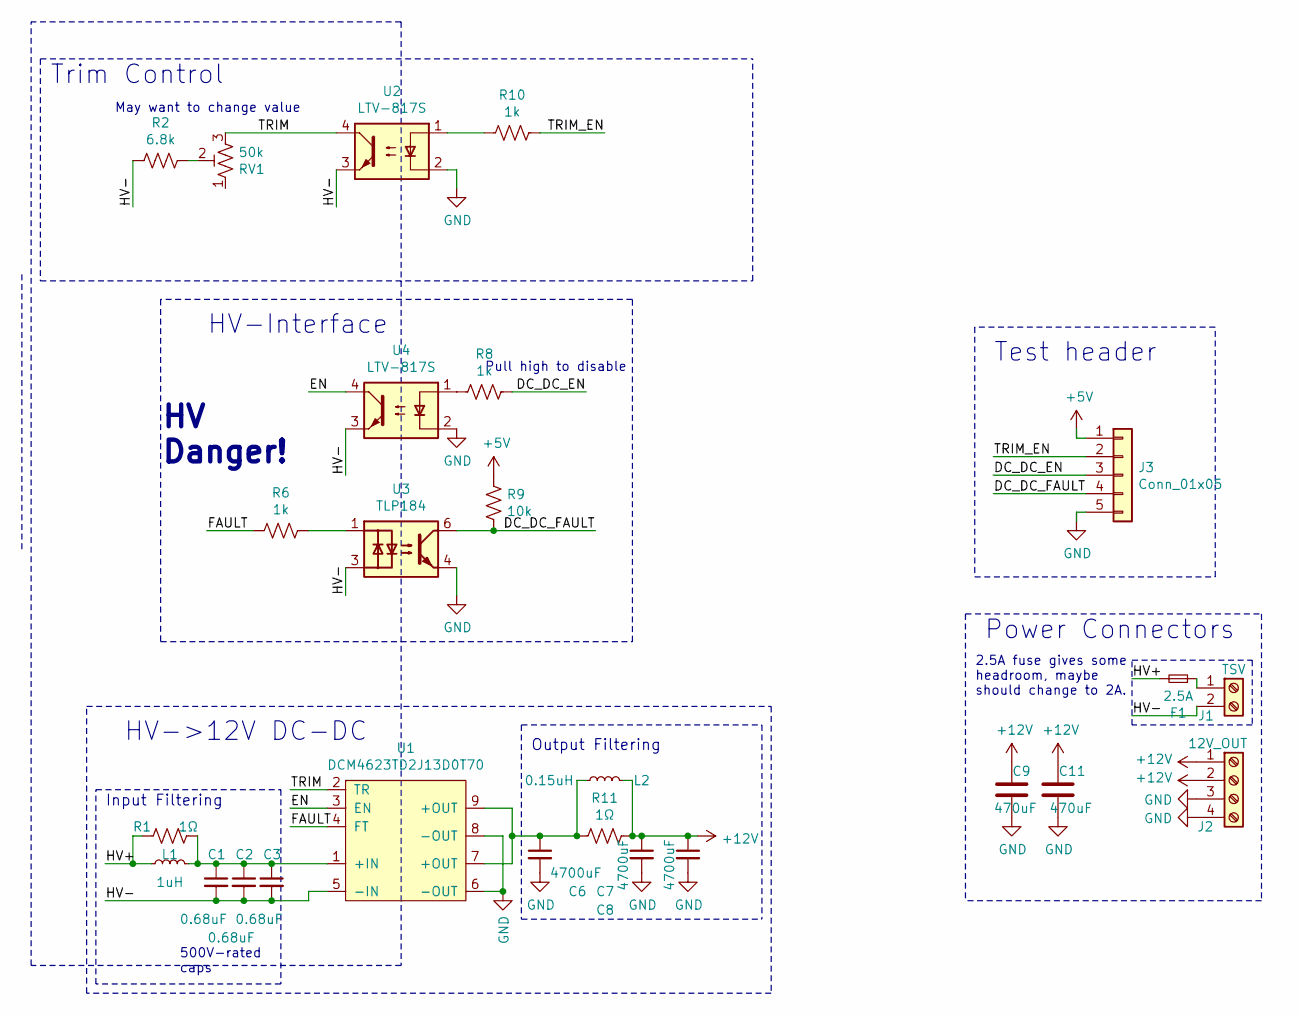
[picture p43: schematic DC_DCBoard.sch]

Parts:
C1, C2, C3: 0.68uF; C_Rect_L18.0mm_W8.0mm_P15.00mm_FKS3_FKP3
C6, C7, C8: 4700uF; CP_Radial_D18.0mm_P7.50mm
C9, C11: 470uF; CP_Radial_D10.0mm_P5.00mm
F1: 2.5A; Fuseholder_Cylinder-5x20mm_Schurter_0031_8201_Horizontal_Op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
J1: TSV; TerminalBlock_MetzConnect_Type067_RT01902HDWC_1x02_P10.00mm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
J2: 12V_OUT; TerminalBlock_MetzConnect_Type067_RT01904HDWC_1x04_P10.00mm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
J3: Conn_01x05; PinHeader_1x05_P2.54mm_Vertical
L1: 1uH; Murata_DFE252012P_Inductor
L2: 0.15uH; PA2607
R1, R11: 1Ω; R_2512_6332Metric
R2: 6.8k; R_0603_1608Metric
R6, R8, R10: 1k; R_0603_1608Metric
R9: 10k; R_0603_1608Metric
RV1: 50k; TC33X-503ECT-ND
U1: DCM4623TD2J13D0T70; DCM4623TD2J13D0T70 w_landpattern
U2, U4: LTV-817S; SMDIP-4_W9.53mm
U3: TLP184; TLP182

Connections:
+5V: J3.1, R9.2
+12V: C7.1, C8.1, C9.1, C11.1, J2.1, J2.2, L2.2, R11.1
/DC_DC_EN: J3.3, R8.1
/DC_DC_FAULT: J3.4, R9.1, U3.6
/EN: U1.3 (EN), U4.4
/FAULT: R6.2, U1.4 (FT)
/HV+: F1.2, L1.1, R1.2
/HV-: C1.2, C2.2, C3.2, J1.2, R2.2, U1.5 (-IN), U2.3, U3.3, U4.3
/TRIM: RV1.3, U1.2 (TR), U2.4
/TRIM_EN: J3.2, R10.1
GND: C6.2, C7.2, C8.2, C9.2, C11.2, J2.3, J2.4, J3.5, U1.6 (-OUT), U1.8 (-OUT), U2.2, U3.4, U4.2
unnamed: C1.1, C2.1, C3.1, L1.2, R1.1, U1.1 (+IN)
unnamed: C6.1, L2.1, R11.2, U1.7 (+OUT), U1.9 (+OUT)
unnamed: F1.1, J1.1
unnamed: R2.1, RV1.2
unnamed: R6.1, U3.1
unnamed: R8.2, U4.1
unnamed: R10.2, U2.1

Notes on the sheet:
500V-rated caps
2.5A fuse gives some headroom, maybe should change to 2A.
Input Filtering
Trim Control
Pull high to disable
Power Connectors
HV->12V DC-DC
HV-Interface
HV Danger!
Output Filtering
May want to change value
Test header

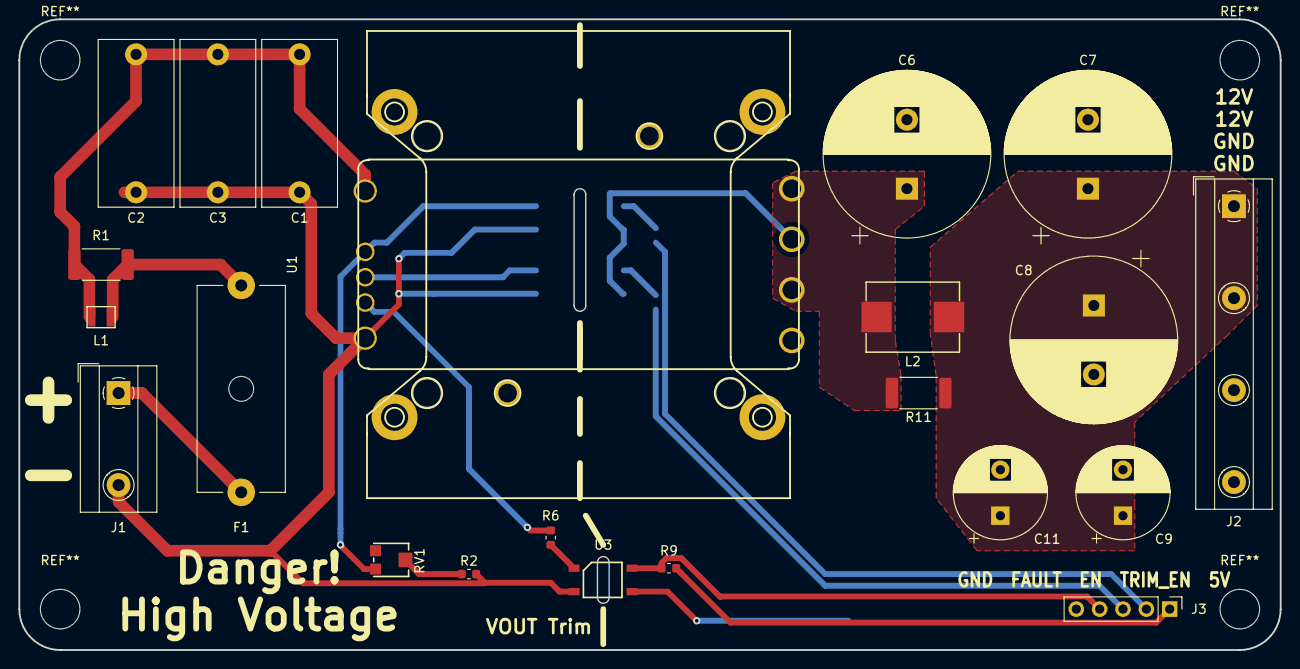
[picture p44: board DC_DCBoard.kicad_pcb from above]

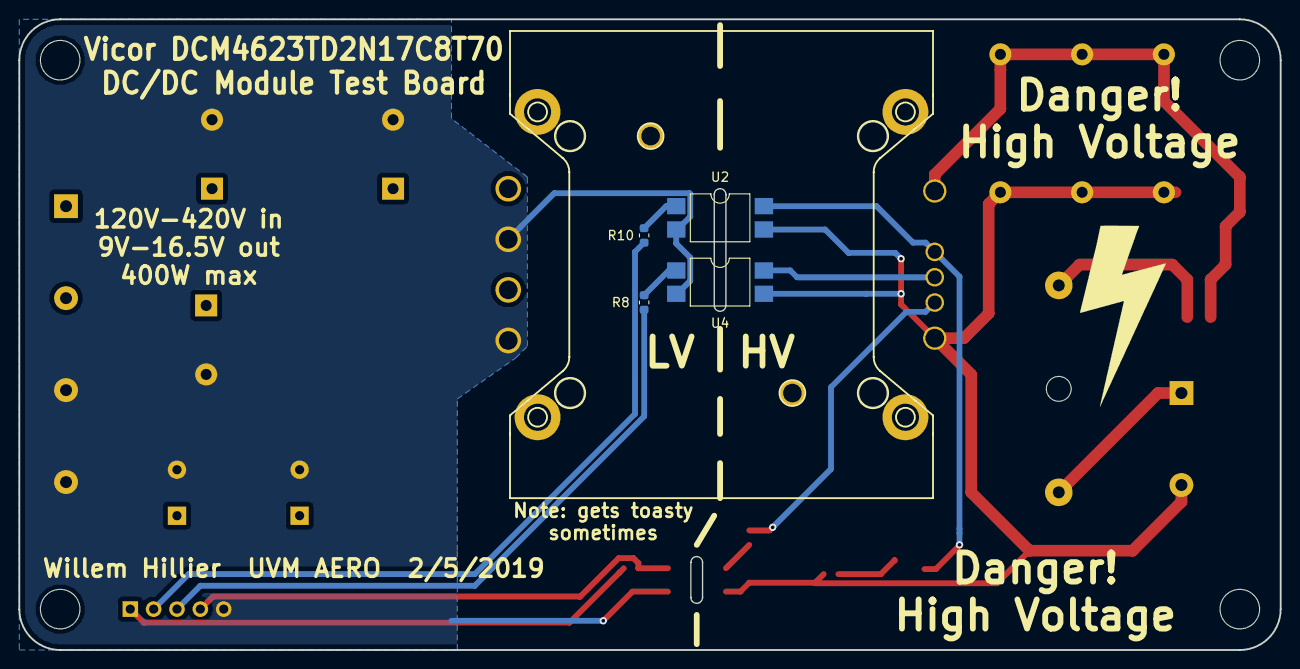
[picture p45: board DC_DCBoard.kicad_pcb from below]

Board: 2 copper layers, 137.2 x 68.6 mm, 26 parts (4 on the bottom side), 18 nets.

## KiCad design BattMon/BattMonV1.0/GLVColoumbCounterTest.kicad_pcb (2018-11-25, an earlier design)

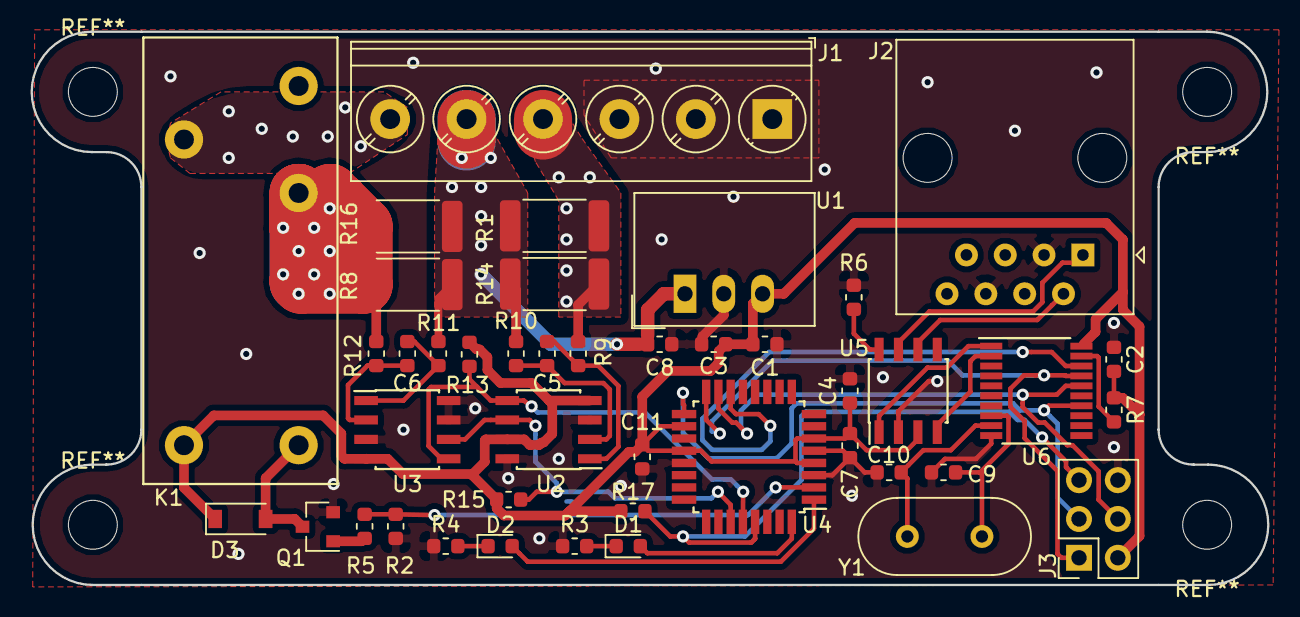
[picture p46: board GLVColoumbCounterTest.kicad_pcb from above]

Board: 2 copper layers, 80.9 x 36.2 mm, 43 parts (0 on the bottom side), 32 nets.

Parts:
C1, C2, C4, C5, C6, C7, C11: 0.1uF; C_0603_1608Metric
C3, C8: 10uF; C_0603_1608Metric
C9, C10: 22pF; C_0603_1608Metric
D1, D2: LED; LED_0603_1608Metric
D3: 1N4148; D_SOD-123
J1: 12V_INTERFACE; TerminalBlock_Phoenix_PT-1,5-6-5.0-H_1x06_P5.00mm_Horizontal
J2: RJ45; RJ45_Amphenol_54602-x08_Horizontal
J3: Conn_02x03_Odd_Even; PinSocket_2x03_P2.54mm_Vertical
K1: G5V-1; G2RL
Q1: MMBT222A; SOT-23
R1, R8, R14, R16: 0.02; R_2512_6332Metric
R2: 100k; R_0603_1608Metric
R3, R4, R5: 1k; R_0603_1608Metric
R6, R7, R15, R17: 10k; R_0603_1608Metric
R9, R10, R11, R12: 10; R_0603_1608Metric
R13: 10K; R_0603_1608Metric
U1: R-78E5.0-0.5; Converter_DCDC_RECOM_R-78E-0.5_THT
U2, U3: INA219; SOIC-8_3.9x4.9mm_P1.27mm
U4: ATmega328P-AU; TQFP-32_7x7mm_P0.8mm
U5: MCP2551-I-SN; SOIC-8_3.9x4.9mm_P1.27mm
U6: MCP2515-IST; TSSOP-20_4.4x6.5mm_P0.65mm
Y1: 8MHz; Crystal_HC49-U_Vertical

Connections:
+5V: C1.1, C2.1, C3.1, C4.1, C7.1, C11.1, D3.1, J3.2, K1.2, R7.1, R13.1, R15.1, R17.1, U1.3, U2.4, U2.7, U3.4, U4.4, U4.6, U4.18, U4.20, U5.3, U6.20
+12V: C8.1, J1.5, R1.1, R8.2, R10.2, R11.2, R14.1, R16.2, U1.1
+BATT: K1.1, R8.1, R12.2, R16.1
/D10: U4.14, U6.18
/LED1: D1.2, U4.32
/LED2: D2.2, U4.1
/LOAD: J1.4, R1.2, R9.2, R14.2
/MISO: J3.1, U4.16, U6.17
/MOSI: J3.4, U4.15, U6.16
/RELAY_CTRL: R2.1, R5.2, U4.2
/RESET: J3.5, R17.2, U4.29
/SCK: J3.3, U4.17, U6.14
/SCL: R13.2, U2.5, U3.5, U4.28
/SDA: R15.2, U2.6, U3.6, U4.27
GND: C1.2, C2.2, C3.2, C4.2, C7.2, C8.2, C9.2, C10.2, C11.2, J1.1, J1.2, J1.3, J2.3, J2.6, J3.6, Q1.2, R2.2, R3.1, R4.1, R6.2, U1.2, U2.3, U2.8, U3.3, U3.7, U3.8, U4.3, U4.5, U4.21, U5.2, U6.10
unnamed: C5.1, R9.1, U2.1
unnamed: C5.2, R10.1, U2.2
unnamed: C6.1, R11.1, U3.1
unnamed: C6.2, R12.1, U3.2
unnamed: C9.1, U6.8, Y1.1
unnamed: C10.1, U6.9, Y1.2
unnamed: D1.1, R3.2
unnamed: D2.1, R4.2
unnamed: D3.2, K1.9, Q1.3
unnamed: J1.6, K1.5
unnamed: J2.1, U5.7
unnamed: J2.2, U5.6
unnamed: Q1.1, R5.1
unnamed: R6.1, U5.8
unnamed: R7.2, U6.19
unnamed: U5.1, U6.1
unnamed: U5.4, U6.2

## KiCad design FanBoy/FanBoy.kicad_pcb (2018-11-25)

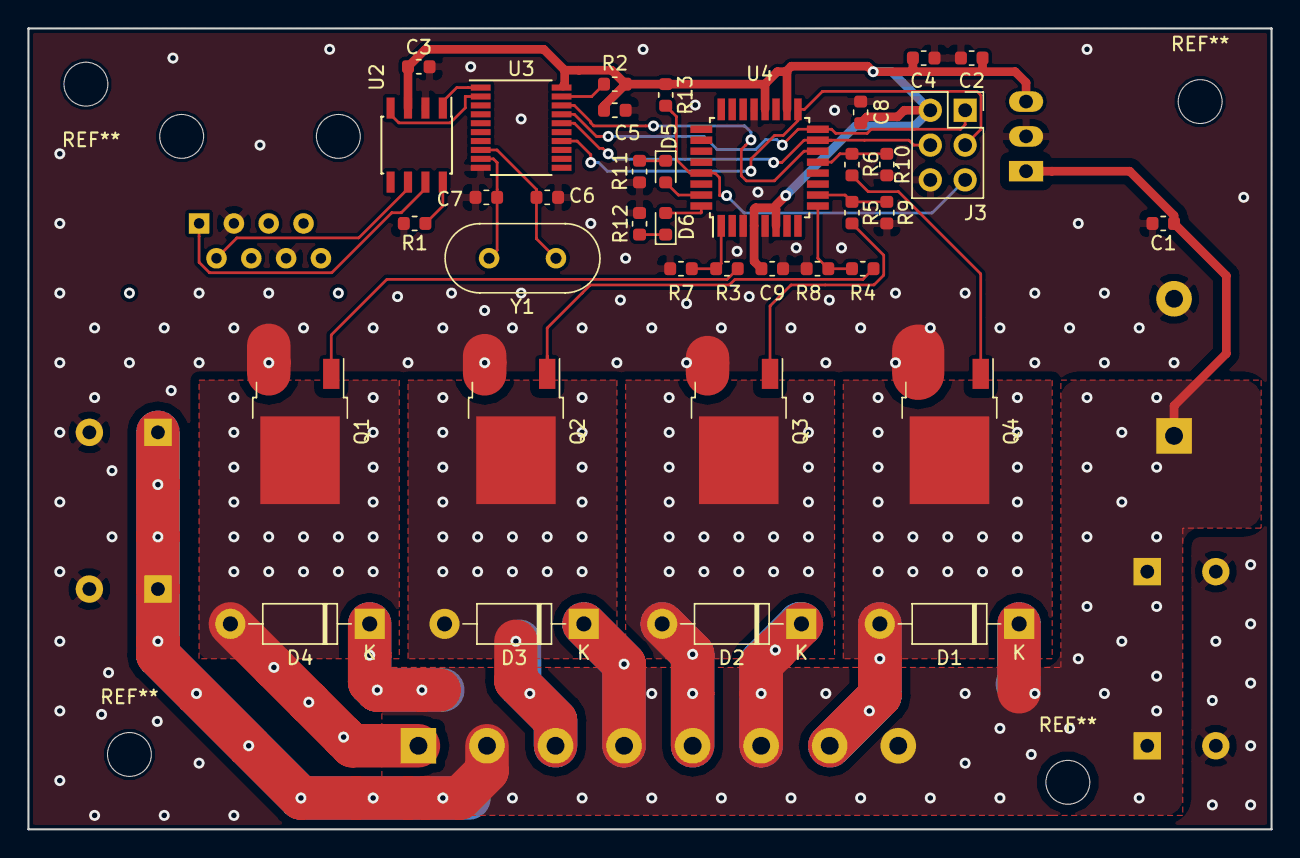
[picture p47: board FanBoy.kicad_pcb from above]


Board: 2 copper layers, 90.7 x 58.4 mm, 45 parts (8 on the bottom side), 32 nets.

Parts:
C1, C4: 10uF; C_0603_1608Metric
C2, C3, C5, C8, C9: 0.1uF; C_0603_1608Metric
C6, C7: 22pF; C_0603_1608Metric
C10, C11, C12, C13: C; CP_Radial_D10.0mm_P5.00mm
D1, D2, D3, D4: D; D_DO-41_SOD81_P10.16mm_Horizontal
D5, D6: LED; LED_0603_1608Metric
J1: RJ45; RJ45_Amphenol_54602-x08_Horizontal
J2: Screw_Terminal_01x02; TerminalBlock_MetzConnect_Type067_RT01902HDWC_1x02_P10.00mm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
J3: Conn_02x03_Odd_Even; PinSocket_2x03_P2.54mm_Vertical
J4: Screw_Terminal_01x08; TerminalBlock_Phoenix_MKDS-1,5-8_1x08_P5.00mm_Horizontal
Q1, Q2, Q3, Q4: Q_NMOS_GDS; TO-252-2
R1, R2, R13: 10k; R_0603_1608Metric
R3, R4, R5, R6, R7, R8, R9, R10: R_US; R_0603_1608Metric
R11, R12: 1k; R_0603_1608Metric
U1: R-78E5.0-0.5; Converter_DCDC_RECOM_R-78E-0.5_THT
U2: MCP2551-I-SN; SOIC-8_3.9x4.9mm_P1.27mm
U3: MCP2515-IST; TSSOP-20_4.4x6.5mm_P0.65mm
U4: ATmega328P-AU; TQFP-32_7x7mm_P0.8mm
Y1: 8MHz; Crystal_HC49-U_Vertical

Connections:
+5V: C2.1, C3.1, C4.1, C5.1, C8.1, C9.1, J3.2, R2.1, R13.1, U1.3, U2.3, U3.20, U4.4, U4.6, U4.18, U4.20
+12V: C1.1, C10.1, C11.1, C12.1, C13.1, D1.1, D2.1, D3.1, D4.1, J2.1, J4.2, J4.4, J4.6, J4.8, U1.1
/CTRL1: R6.1, R10.2, U4.13
/CTRL2: R5.1, R9.2, U4.10
/CTRL3: R4.1, R8.2, U4.9
/CTRL4: R3.2, R7.2, U4.1
/D10: U3.18, U4.14
/LED1: D5.2, U4.31
/LED2: D6.2, U4.32
/LOAD1: D1.2, J4.7, Q4.2
/LOAD2: D2.2, J4.5, Q3.2
/LOAD3: D3.2, J4.3, Q2.2
/LOAD4: D4.2, J4.1, Q1.2
/MISO: J3.1, U3.17, U4.16
/MOSI: J3.4, U3.16, U4.15
/RESET: J3.5, R13.2, U4.29
/SCK: J3.3, U3.14, U4.17
GND: C1.2, C2.2, C3.2, C4.2, C5.2, C6.2, C7.2, C8.2, C9.2, C10.2, C11.2, C12.2, C13.2, J1.3, J1.6, J2.2, J3.6, Q1.3, Q2.3, Q3.3, Q4.3, R1.2, R7.1, R8.1, R9.1, R10.1, R11.1, R12.1, U1.2, U2.2, U3.10, U4.3, U4.5, U4.21
unnamed: C6.1, U3.8, Y1.1
unnamed: C7.1, U3.9, Y1.2
unnamed: D5.1, R11.2
unnamed: D6.1, R12.2
unnamed: J1.1, U2.7
unnamed: J1.2, U2.6
unnamed: Q1.1, R3.1
unnamed: Q2.1, R4.2
unnamed: Q3.1, R5.2
unnamed: Q4.1, R6.2
unnamed: R1.1, U2.8
unnamed: R2.2, U3.19
unnamed: U2.1, U3.1
unnamed: U2.4, U3.2

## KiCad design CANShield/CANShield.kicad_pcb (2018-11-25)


Board: 2 copper layers, 69.1 x 53.8 mm, 21 parts (1 on the bottom side), 15 nets.

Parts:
A1: Arduino_UNO_R3; Arduino_UNO_R3_WithMountingHoles
C1, C3: 10uF; C_0603_1608Metric
C2, C4, C5: 0.1uF; C_0603_1608Metric
C6, C7: 22pF; C_0603_1608Metric
J1: RJ45; RJ45_Amphenol_54602-x08_Horizontal
R1, R2: 10k; R_0603_1608Metric
TP1, TP2, TP3, TP4, TP5, TP6: TestPoint; TestPoint_Pad_2.5x2.5mm
U1: R-78E5.0-0.5; Converter_DCDC_RECOM_R-78E-0.5_THT
U2: MCP2551-I-SN; SOIC-8_3.9x4.9mm_P1.27mm
U3: MCP2515-IST; TSSOP-20_4.4x6.5mm_P0.65mm
Y1: 8MHz; Crystal_HC49-U_Vertical

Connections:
+5V: A1.5, C2.1, C3.1, C4.1, C5.1, R2.1, U1.3, U2.3, U3.20
+12V: C1.1, U1.1
GND: A1.6, A1.7, A1.29, C1.2, C2.2, C3.2, C4.2, C5.2, C6.2, C7.2, J1.3, J1.6, R1.2, U1.2, U2.2, U3.10
unnamed: C6.1, U3.8, Y1.1
unnamed: C7.1, U3.9, Y1.2
unnamed: J1.1, TP1.1, U2.7
unnamed: J1.2, TP2.1, U2.6
unnamed: J1.4, TP3.1
unnamed: J1.5, TP4.1
unnamed: J1.7, TP5.1
unnamed: J1.8, TP6.1
unnamed: R1.1, U2.8
unnamed: R2.2, U3.19
unnamed: U2.1, U3.1
unnamed: U2.4, U3.2

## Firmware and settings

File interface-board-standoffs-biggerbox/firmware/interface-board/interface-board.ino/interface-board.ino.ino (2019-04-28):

/*Willem Hillier, UVM AERO, 2019. For CS4 cooling/interface box.
  TODO:
    -Brakelight control off of pressure sensor data on CAN.
    -Temp curve control over CAN/storing in EEPROM
*/

#include <Adafruit_INA219.h>
#include <SPI.h>
#include "mcp_can.h"
#include <avr/wdt.h>
#include <avr/interrupt.h>
#define DEBUG

//CAN ID defines
#define ID_BASE               0x62
#define ID_RESET              ID_BASE
#define ID_PROG_SELECT        ID_BASE + 1
#define ID_PROG_WRITE         ID_BASE + 2
#define ID_PROG_DONE          ID_BASE + 3
#define ID_PROG_ERROR         ID_BASE + 4
#define ID_STATUS             ID_BASE + 5
#define ID_TEST               ID_BASE + 6
#define ID_DC_DC_FAULT        ID_BASE + 7

//External CAN defines
#define ID_RMC_TEMPS1          0xA0
#define ID_RMC_TEMPS2          0xA1
#define ID_RMC_TEMPS3          0xA2
#define ID_DASH_COOLING_EN     0x6F
#define ID_PEDAL_BOARD_DATA    0x32 //Byte 3 and 2 are brake pressure, same format as reinhart temps
#define ID_PEDAL_BOARD_PRECHARGE_STATUS 0x36

//NTC Constants
#define SERIESRESISTOR         10000
#define NOMINAL_RESISTANCE     10000
#define NOMINAL_TEMPERATURE    25
#define BCOEFFICIENT           3380

//Timing constants
#define HEARTBEAT_INTERVAL     500
#define DC_DC_REBOOT_DELAY     2000
#define DASH_STATUS_TIMEOUT    2000

//DC-DC Levels
#define DC_DC_FAULT_LVL        0
#define DC_DC_EN_LVL           0

//Cooling constants
#define RADIATOR_FAN_MAX_TEMP  35
#define RADIATOR_FAN_MIN_TEMP  23
#define MIN_RADIATOR_FAN_VAL   64 //Out of 255
#define INTERNAL_FAN_MIN_TEMP  25
#define INTERNAL_FAN_MAX_TEMP  50
#define MIN_INTERNAL_FAN_VAL   64 //Out of 255
#define PUMP_ON_TEMP           5
#define PUMP_OFF_TEMP          0  //Change back to 21 C

//Pin defines
#define SPI_CAN_CS             6
#define LED1                   14      //blue led
#define LED2                   2       //green led
#define INTERNAL_FAN_0         9       //Internal fan header
#define RADIATOR_FAN_1         10      //Radiator fans
#define PUMP                   3       //Cooling pump
#define BRAKE_LIGHT_3          5       //Nothing yet
#define NTC1                   A1
#define NTC2                   A2
#define DC_DC_EN               4
#define DC_DC_FAULT            7
#define DC_DC_TR_EN            8

//Misc. defines
#define BRAKELIGHT_THRESHOLD   500

MCP_CAN CAN(SPI_CAN_CS);     // Set CS pin

Adafruit_INA219 ina219;

uint32_t lastheartbeatTime;
uint32_t lastDCDCFaultTime;
uint32_t dashCoolingStatusRecievedTime;

bool coolingEnabled = 1;
bool dashCoolingStatusRecieved = 0;
bool prechargeComplete = 0;
bool fansRamped = 0;
int16_t RMCTemps[11];       //Motor controller temps, equivilent to the following:
/*
  int RMCTempA     = 0;  //IGBT phase A
  int RMCTempB     = 0;  //IGBT phase B
  int RMCTempC     = 0;  //IGBT phase C
  int RMCTempGDB   = 0;  //gate driver board
  int RMCTempCB    = 0;  //control board
  int RMCTempRTD1  = 0;  //RTD input 1
  int RMCTempRTD2  = 0;  //RTD input 2
  int RMCTempRTD3  = 0;  //RTD input 3
  int RMCTempRTD4  = 0;  //RTD input 4
  int RMCTempRTD5  = 0;  //RTD input 5
  int RMCTempMotor = 0;  //filtered temp value from motor temp sensor
*/

void setup() {

  //Disable Vicor
  pinMode(DC_DC_EN, OUTPUT);
  digitalWrite(DC_DC_EN, !DC_DC_EN_LVL);
  pinMode(DC_DC_TR_EN, OUTPUT);

#ifdef DEBUG
  Serial.println();
  Serial.println("setup()");
#endif

  //Internal fan PWM frequency
  TCCR1B = TCCR1B & B11111000 | B00000001; // set timer 1 divisor to 1 for PWM frequency of 31372.55 Hz

  pinMode(SPI_CAN_CS, OUTPUT);
  pinMode(LED1, OUTPUT);
  pinMode(LED2, OUTPUT);

  //Set pinmodes and immediately turn off
  pinMode(INTERNAL_FAN_0, OUTPUT);
  analogWrite(INTERNAL_FAN_0, 0);

  pinMode(RADIATOR_FAN_1, OUTPUT);
  analogWrite(RADIATOR_FAN_1, 0);

  pinMode(PUMP, OUTPUT);
  digitalWrite(PUMP, 0);

  pinMode(BRAKE_LIGHT_3, OUTPUT);
  digitalWrite(BRAKE_LIGHT_3, 0);

  Serial.begin(115200);

  lastheartbeatTime = millis(); //Used for sending out status/temps/voltage/current/heartbeat over CAN on a regular interval

  //Current monitoring startup
  ina219.begin();
  ina219.setCalibration_32V_1A();
  delay(100);

  while (CAN_OK != CAN.begin(CAN_500KBPS)) { //Check we can talk to CAN
#ifdef DEBUG
    Serial.println("CAN BUS Shield init fail");
    Serial.println("Init CAN BUS Shield again");
#endif
    delay(100);
  }
#ifdef DEBUG
  Serial.println("CAN BUS Shield init ok!");
#endif

  digitalWrite(LED2, HIGH);
  //Fade brake light up and down to indicate sucessful initialization
  for (int i = 0; i < 255; i = i + 5) {
    analogWrite(BRAKE_LIGHT_3, i);
    delay(10);
  }
  for (int i = 255; i > 0; i = i - 5) {
    analogWrite(BRAKE_LIGHT_3, i);
    delay(10);
  }
  digitalWrite(BRAKE_LIGHT_3, 0);
}

void testRoutine() {
  Serial.println();
  Serial.println("testRoutine()");

  //Shut down everything
  analogWrite(INTERNAL_FAN_0, 0);
  analogWrite(RADIATOR_FAN_1, 0);
  digitalWrite(PUMP, 0);
  digitalWrite(BRAKE_LIGHT_3, 0);

  //Test routine
  delay(1000);

  //Internal fans
  Serial.println("Testing internal fans.");
  analogWrite(INTERNAL_FAN_0, 255);
  delay(3000);
  analogWrite(INTERNAL_FAN_0, 0);

  //Radiator fans
  Serial.println("Testing radiator fans.");
  for (int i = 0; i < 255; i = i + 5) {
    analogWrite(RADIATOR_FAN_1, i);
    delay(20);
  }
  delay(3000);
  analogWrite(RADIATOR_FAN_1, 0);

  //Cooling pump
  Serial.println("Testing cooling pump.");
  digitalWrite(PUMP, HIGH);
  delay(3000);
  digitalWrite(PUMP, LOW);

  //Brake light
  Serial.println("Testing brake light.");
  digitalWrite(BRAKE_LIGHT_3, HIGH);
  delay(3000);
  digitalWrite(BRAKE_LIGHT_3, LOW);

  //NTCs
  Serial.println("Testing NTCs.");
  Serial.print("NTC 1 Temp (deg C): ");
  Serial.println(calculateTemperatureC(analogRead(NTC1)));
  Serial.print("NTC 2 Temp (deg C): ");
  Serial.println(calculateTemperatureC(analogRead(NTC2)));

  //LEDs
  Serial.println("Testing LEDs.");

  Serial.println("LED1");
  digitalWrite(LED1, HIGH);
  delay(1000);
  digitalWrite(LED1, LOW);

  Serial.println("LED2");
  digitalWrite(LED2, HIGH);
  delay(1000);
  digitalWrite(LED2, LOW);

}

float calculateTemperatureC(float adcReading) {
#ifdef DEBUG
  Serial.println();
  Serial.println("calculateTemperatureC");
#endif

  //Old code
  //float NTCResistance = R_DIVIDER * ((DMAX / adcReading) - 1);
  //float tKelvin = 1 / (NTC_T_ROOM + NTC_BETA * log(NTC_R_ROOM / NTCResistance));

  float Resistance;
  //convert value to resistance
  Resistance = (1023 / (1023 - adcReading)) - 1;
  Resistance = SERIESRESISTOR / Resistance;

  float steinhart;
  steinhart = Resistance / NOMINAL_RESISTANCE;       // (R/Ro)
  steinhart = log(steinhart);                        // ln(R/Ro)
  steinhart /= BCOEFFICIENT;                         // 1/B * ln(R/Ro)
  steinhart += 1.0 / (NOMINAL_TEMPERATURE + 273.15); // + (1/To)
  steinhart = 1.0 / steinhart;                       // Invert
  steinhart -= 273.15;                               // convert to C

#ifdef DEBUG
  Serial.println("Calculating temperature");
  Serial.print("adcReading: ");
  Serial.print(adcReading, DEC);
  Serial.print(", temperature deg C: ");
  Serial.println(steinhart);
#endif

  return (steinhart);
}

void updateFansFromTemps() {
#ifdef DEBUG
  Serial.println();
  Serial.println("updateFansFromTemps()");
#endif

  //Print temps
#ifdef DEBUG
  for (int i = 0; i < 11; i++) {
    Serial.println(RMCTemps[i]);
  }
#endif

  //Find max temp
  float maxTemp = 0;
  //Change back to i<5
  for (int i = 0; i < 3; i++) {
    if (maxTemp < RMCTemps[i]) {
      maxTemp = RMCTemps[i];
    }
  }

  maxTemp = maxTemp / 10; //Reinhart temps are 10x actual

#ifdef DEBUG
  Serial.print("maxTemp: ");
  Serial.println(maxTemp);
#endif

  if (coolingEnabled == 1 && prechargeComplete == 1) {
    //First time starting fans?
    if (fansRamped == 0) {
      Serial.println("Ramping radiator fans.");
      for (int i = 0; i < 255; i = i + 5) {
        analogWrite(RADIATOR_FAN_1, i);
        delay(20);
      }
      fansRamped = 1;
    } else {
      //Radiator fan control
      analogWrite(RADIATOR_FAN_1, map(maxTemp, RADIATOR_FAN_MIN_TEMP, RADIATOR_FAN_MAX_TEMP, 0, 255)); //TODO: Check mapping

      //Pump control with deadband
      if (maxTemp > PUMP_ON_TEMP) { //TODO: Check mapping
#ifdef DEBUG
        Serial.print("Pump on.");
#endif
        digitalWrite(PUMP, 1);
      }
      else if (maxTemp < PUMP_OFF_TEMP) {
#ifdef DEBUG
        Serial.print("Pump off.");
#endif
        digitalWrite(PUMP, 0);
      }

      //Local fan control from NTC2
      //Average samples
      int NTC2val = analogRead(NTC2);
      for (int i = 0; i < 9; i++) {
        NTC2val = analogRead(NTC2) + NTC2val;
      }
      float NTC2Temp = calculateTemperatureC(NTC2val / 9);

      Serial.println(NTC2Temp);
      int fanval = map(NTC2Temp, INTERNAL_FAN_MIN_TEMP, INTERNAL_FAN_MAX_TEMP, 0, 255);
      Serial.println(fanval);
      fanval = min(fanval, 255);
      fanval = max(fanval, MIN_INTERNAL_FAN_VAL);
      Serial.println(fanval);
      analogWrite(INTERNAL_FAN_0, fanval);
      //If cooling disabled
    }
  } else {
    analogWrite(RADIATOR_FAN_1, 0);
    digitalWrite(PUMP, LOW);
  }
}

void reportVoltageCurrentTemps() {
#ifdef DEBUG
  Serial.println();
  Serial.println("reportVoltageCurrentTemps()");
#endif

  uint16_t voltage_mV = ina219.getBusVoltage_V();
  uint16_t current_mA = ina219.getCurrent_mA();

#ifdef DEBUG
  Serial.print("voltage_mV: ");
  Serial.print(voltage_mV);
  Serial.print(", current_mA: ");
  Serial.println(current_mA);
#endif

  //Example CAN message data: 0x3D   0x35   0x5B   0x57   0x00      0x00      0x00      0x00
  //                          V_LSB  V_MSB  A_LSB  A_MSB  NTC1_LSB  NTC1_MSB  NTC2_LSB  NTC2_MSB
  //Here, 13.629V and 22.363A
  unsigned char bufToSend[8] = {0, 0, 0, 0, 0, 0, 0, 0};
  bufToSend[0] = voltage_mV & 0xFF;
  bufToSend[1] = voltage_mV >> 8;
  bufToSend[2] = current_mA & 0xFF;
  bufToSend[3] = current_mA >> 8;

  //Report internal temps on CAN
  //TODO: Map values to temp properly
  uint16_t NTC1Temp = 100 * calculateTemperatureC(analogRead(NTC1));
  uint16_t NTC2Temp = 100 * calculateTemperatureC(analogRead(NTC2));
  bufToSend[4] = NTC1Temp;
  bufToSend[5] = NTC1Temp >> 8;
  bufToSend[6] = NTC2Temp;
  bufToSend[7] = NTC2Temp >> 8;

#ifdef DEBUG
  Serial.print("bufToSend: ");
  for (int i = 0; i < 8; i++) {
    Serial.print(bufToSend[i], HEX);
    Serial.print(" ");
  }
  Serial.println();
#endif

  CAN.sendMsgBuf(ID_STATUS, 0, 8, bufToSend);
}

void filterCan(unsigned long canId, unsigned char buf[8]) { //Decides what to do with CAN data
#ifdef DEBUG
  // Serial.println();
  // Serial.print("filterCan(): ");
#endif

  switch (canId) {
    case ID_RMC_TEMPS1:
#ifdef DEBUG
      Serial.print("ID_RMC_TEMPS1");
#endif
      for (int i = 0; i < 4; i++) {
        RMCTemps[i] = ((buf[2 * i + 1] << 8) | buf[2 * i]); //Place temps into RMCTemps
      }
      break;

    case ID_RMC_TEMPS2:
#ifdef DEBUG
      Serial.print("ID_RMC_TEMPS2");
#endif

      for (int i = 0; i < 4; i++) {
        RMCTemps[i + 4] = ((buf[2 * i + 1] << 8) | buf[2 * i]);  //Place temps into RMCTemps
      }
      break;

    case ID_RMC_TEMPS3:
#ifdef DEBUG
      Serial.print("ID_RMC_TEMPS3");
#endif

      for (int i = 0; i < 3; i++) {
        RMCTemps[i + 8] = ((buf[2 * i + 1] << 8) | buf[2 * i]);  //Place temps into RMCTemps
      }
      break;
    case ID_DASH_COOLING_EN:
      dashCoolingStatusRecievedTime = millis();
      dashCoolingStatusRecieved = 1;
      if (buf[0] == 1) {
#ifdef DEBUG
        Serial.print("coolingEn");
#endif
        coolingEnabled = 1;
        //Soft-start radiator fans
        //for (int i = 0; i < MIN_RADIATOR_FAN_VAL; i = i + 5) {
        //  analogWrite(INTERNAL_FAN_0, i);
        //  delay(100);
        //}
      } else if (buf[0] = 0) {
        Serial.print("coolingDis");
        coolingEnabled = 0;
      }

#ifdef DEBUG
      Serial.println("ID_DASH_COOLING_EN");
#endif
      break;
    case ID_TEST:
      testRoutine();
      break;
    case ID_RESET:
      cli();
      wdt_enable(WDTO_15MS);
      while (1);
    case ID_PEDAL_BOARD_PRECHARGE_STATUS:
      //If precharge is complete, enable Vicor
      if (buf[0] == 2) {
        prechargeComplete = 1;
        digitalWrite(DC_DC_EN, DC_DC_EN_LVL);
      } else {
        prechargeComplete = 0;
        digitalWrite(DC_DC_EN, !DC_DC_EN_LVL);
      }
      break;
    case ID_PEDAL_BOARD_DATA:{
     uint16_t brakePressure = (buf[3] << 8) | buf[2];
      if (brakePressure > BRAKELIGHT_THRESHOLD) {
        digitalWrite(BRAKE_LIGHT_3, HIGH);
      } else {
        digitalWrite(BRAKE_LIGHT_3, LOW);
      }
      break;
    }
    default:
#ifdef DEBUG
      //Serial.println("ID_UNKNOWN");
#endif
      break;
  }
}

void loop() {
  unsigned char len = 0;
  unsigned char buf[8];

  if (CAN_MSGAVAIL == CAN.checkReceive()) {   // check if data coming
    CAN.readMsgBuf(&len, buf);    // read data,  len: data length, buf: data buf

    filterCan(CAN.getCanId(), buf);
  }
  //If we haven't recieved a cooling enabled status message from dash in more than DASH_STATUS_TIMEOUT, then run pumps/fans at 50%
  /*if (millis() > dashCoolingStatusRecievedTime + DASH_STATUS_TIMEOUT) {
    analogWrite()
    }
  */
  //If it's time to check DC/DC status (done every DC_DC_REBOOT_DELAY milliseconds)
  //Make sure precharging is complete before trying to reboot DC/DC
  if ((millis() > lastDCDCFaultTime + DC_DC_REBOOT_DELAY) && (prechargeComplete == 1)) {
    //Check for fault
    if (digitalRead(DC_DC_FAULT) == DC_DC_FAULT_LVL) {
      Serial.println("fault");
      //reportDCDCFault();
      //turn off DC/DC
      digitalWrite(DC_DC_EN, !DC_DC_EN_LVL);
    }
    digitalWrite(DC_DC_EN, DC_DC_EN_LVL);
    lastDCDCFaultTime = millis();
  }

  if (millis() > lastheartbeatTime + HEARTBEAT_INTERVAL) {
#ifdef DEBUG
    Serial.println("updating lastheartbeatTime");
#endif
    lastheartbeatTime = millis();
    updateFansFromTemps(); //Updates all cooling fan speeds + pump enable according to temps
    reportVoltageCurrentTemps();
    //TODO: checkAndReportDCDCStatus();
  }
}

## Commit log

2019-01-25 Created interface-board
    [interface-board.kicad_pcb, interface-board.sch]
2019-01-25 Lots of interface-board layout done
    [file5C5EE840.sch, file5C667FAE.sch, interface-board.sch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]
2019-01-25 interface-board getting there schematic-wise.
    [file5C4BAF40.sch, file5C5EE840.sch, file5C667FAE.sch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]
2019-01-25 schematic almost done maybe hopefully
    [file5C667FAE.sch, interface-board.sch, uC+CAN.sch]
2019-01-25 more interface-board
    [file5C4BAF40.sch, file5C5EE840.sch, file5C667FAE.sch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]
2019-01-26 Beginnings of board layout of interface-board
    [benderProjection.dxf, file5C4BAF40.sch, file5C5EE840.sch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]
2019-01-27 Updated main connector and pinout
    [40098.STEP, 40258.step, 40261.STEP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]
2019-01-28 Added IMD LV connector
    [_saved_interface-board.sch, interface-board.kicad_pcb, interface-board.sch]
2019-01-29 Fixed more shit
    [interface-board.kicad_pcb, interface-board.sch]
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2019-02-05 did some stuff
    [c-1-776087-1-l-3d-colored.STEP, c-1-776087-1-l-3d.SLDPRT, interface-board.kicad_pcb]
2019-02-06 Made DC/DC test board
    [40098.STEP, 40258.step, 40261.STEP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]
2019-02-06 Made PDF schematic of DC/DC test board
    [DC_DCBoard.sch]
2019-02-06 Fixed pot value on test board
    [DC_DCBoard.kicad_pcb, DC_DCBoard.sch, TC-33X-2.stp]
2019-02-06 updated footprints
    [DC_DCBoard.kicad_pcb, TC-33X-2.stp]
2019-02-06 updated test-board
    [interface-board.kicad_pcb]
2019-02-06 Footprints centralized now
    [interface-board.kicad_pcb]
2019-02-09 Getting there with layout of big board...
    [31-8201.SLDPRT, 31-8201.STEP, 32436_vicor_spring.STEP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]
2019-02-09 Interface-board largely routed
    [DC_DCBoard.kicad_pcb, file5C4BAF40.sch, file5C667FAE.sch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]
2019-02-10 Fully routed, added blinky DC/DC, added silkscreen labels, bumped 5V traces up to 0.025"
    [EPM(EE22)-S-0.STEP, interface-board.kicad_pcb, interface-board.sch]
2019-02-12 Cleaned up 3d models
    [EPM(EE22)-S-0.SLDPRT, EPM(EE22)-S-0.STEP, IC_Toshiba_TLP185_SE_eec.STEP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]
2019-02-13 Updated 3d footprints on testboard
    [DC_DCBoard.kicad_pcb]
2019-02-15 Added board images for interface-board
    [interface-board.kicad_pcb]
2019-02-22 Made LED indicator.
    [60v-indicator-led.kicad_pcb, 60v-indicator-led.sch, interface-board.kicad_pcb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]
2019-03-05 Put Vicor on a removable module
    [DC_DCBoard.sch, benderProjection.dxf, file5C4BAF40.sch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]
2019-03-06 Board probably ready to ship.
    [_saved_interface-board.sch, benderProjection.dxf, file5C4BAF40.sch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]
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2019-03-07 Made lots of gerbers, shipped boards.
    Also, re-routed interface-board to be 8/8mil minimum spacing.
    [c-1-770166-0-n-3d.stp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]
2019-03-17 made iBom for assembly and current schematic pdf
    [interface-board.kicad_pcb]
2019-03-27 Beginning of interface-board, moved around interface-board files for better organization
    [_saved_interface-board.sch, benderProjection.dxf, file5C4BAF40.sch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]
2019-03-28 Fixed firmware folder
    [_saved_interface-board.sch, benderProjection.dxf, file5C4BAF40.sch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]
2019-03-30 Made BOM etc for 60v-indicator-led
    [v2-bom.csv, v2.kicad_pcb, v2.sch]
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2019-04-04 Made rev1.1 of interface-board
    Added i2c pullups, fixed chip pinout, added isolation slot, removed secondary DC/DC converter
    [file5C4BAF40.sch, file5C5EE840.sch, file5C83278D.sch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]
2019-04-05 Shipped interface-board-standoffs-biggerbox
    [benderProjection.dxf, file5C4BAF40.sch, file5C5EE840.sch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]
2019-04-15 Cleaned up drawings.user laser on interface-board, and made iBom for assembly.
    [file5C83278D.sch, interface-board.kicad_pcb]
2019-04-20 Fully working interface-board firmware, fixed wrong polarity on vicor-socket
    [interface-board.sch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]
2019-04-26 Fixed lots of stuff for interface-board. It works now.
    Still need to implement brake light control and debug cooling switch logic because it don't work
    [interface-board.ino.ino]
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2019-05-08 Started making TSAL-driver PCB
    [TSAL-driver.kicad_pcb, TSAL-driver.sch]
2019-06-25 Drew fet inverter
    [TSAL-driver.sch]
2019-07-10 More work on TSAL-driver.
    TODO: Get actual values in for both 555 circuits.
    [TSAL-driver.sch]
2019-07-17 TODO: update values for 555 blinker
    [TSAL-driver.sch]
2019-08-16 Beginning of can-game-controller
    An interface to drive a simulator with the real car.
    [TSAL-driver.sch, can-game-controller.kicad_pcb, can-game-controller.sch]
2019-08-18 Finished USB CANBUS game controller
    Will allow us to use the car as a game controller for a simulator
    [can-game-controller.sch]
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2019-09-10 Added footprints for tsal-driver
    [TSAL-driver.kicad_pcb, TSAL-driver.sch]
2019-09-11 Started laying out TSAL-driver
    [TSAL-driver.kicad_pcb, TSAL-driver.sch]
2019-09-11 Moved capictor
    [TSAL-driver.kicad_pcb]
2019-09-12 Organized TSAL-Driver board
    [TSAL-driver.kicad_pcb]
2019-09-16 Inputs and Outputs are on Opposite Sides
    [TSAL-driver.kicad_pcb]
2019-10-04 New TSAL Schematic
    Schematic complete, on to annotations
    [TSAL-driver.sch]
2019-10-08 Made Game Controller BOM
    [can-game-controller.csv]
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2019-10-08 started choosing footprints
    [TSAL-driver.sch]
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2019-10-09 Cleaned up board, added 3D
    [TSAL-driver-B_Cu.gbr, TSAL-driver-B_Mask.gbr, TSAL-driver-B_Paste.gbr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]
2019-10-09 Fixed 3d
    [TSAL-driver.kicad_pcb]
2019-10-09 Added 3D for terminals, cleaned up old 3d
    [TSAL-driver.kicad_pcb]
2019-10-09 New LDB footprint
    Completed TSAL
    [TSAL-driver.kicad_pcb, TSAL-driver.sch]
2019-10-15 Start work on port panel
    [port-panel.kicad_pcb, port-panel.sch]
2019-10-21 Work on port panel
    [port-panel.sch]
2019-10-24 Demo Board RGB LED
    [demo-board.kicad_pcb, demo-board.sch]
2019-10-25 Demo Board updated. Ready for Review
    [demo-board.kicad_pcb, demo-board.sch, demo-board_panelized.kicad_pcb]
2019-11-01 Work on USB Hub
    [USBHUB.sch, port-panel.sch]
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
